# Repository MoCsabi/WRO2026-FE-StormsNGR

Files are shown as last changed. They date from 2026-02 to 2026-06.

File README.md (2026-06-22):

# Introduction
We are the StormsNGR team from Hungary, and we are competing in the 2026 WRO Future Engineers category. This is our third year after two very successful years of competition. You can find our documentation from 2024 [here](https://github.com/MoCsabi/WRO2024-FE-StormsNGR) (🥇) and from 2025 [here](https://github.com/MoCsabi/WRO2025-FE-StormsNGR) (🥉). We will be updating this repository with our progress, which will be documented in our new [Engineering Journal](/Engineering%20Journal.md).

## The team
>Team members
- **Csaba Molnár** from [Budapest University of Technology and Economics](https://www.bme.hu/en) Faculty of Electrical Engineering and Informatics
  - csabi@molnarnet.hu
- **András Gräff** from [Budapest University of Technology and Economics](https://www.bme.hu/en) Faculty of Mechanical Engineering
  - andrasgraff@gmail.com
- **Levente Molnár** from [Vocational Technical School and High School of Biatorbágy](https://en.bit-edu.hu/)
  - levente@molnarnet.hu
>Coach
- József Balázs Gräff
  - graffjozsefb@gmail.com

Links to our socials:

- **Facebook**: https://www.facebook.com/stormsteam/
  - Here you can find updates about the team
- **YouTube**: https://www.youtube.com/channel/UCyzm_Su7qoRCof-ZpbG_9Ig
  - Here you can watch videos about past competitions
- **Instagram**: https://www.instagram.com/storms_team_hun/
  - Cool posts and updates about our, and our sister-team StormsRMS' preparation for upcoming competitions

# Abstract
Our solution is an autonomous car powered by a Raspberry Pi coded in Python, responsible for the main challenge logic, and an ESP microcontroller coded in C, responsible for controlling the motors and processing sensor data. The two devices communicate using UART. We use a 360° 2D LiDAR combined with a gyro to always know where the robot is on the mat. Detection of the traffic sign's color is done by combining the output of the LiDAR with the camera feed to know exactly where the object is. We use ackermann steering geometry calibrated so the car can leave the parking space in one continuous arc. Driving is powered by 1 DC motor through a differential gearbox designed from scratch, with a top speed of around 2.6 m/s.

# Table of contents

### [Our journey](/Our%20Journey.md)
### [Engineering Journal](/Engineering%20Journal.md)
### [Ideas and principles](/Ideas_and_principles.md)
### [Mobility and Mechanical Design, Power and Sensor Architecture documentation](/schemes/README.md)
### [Software Architecture and Obstacle Strategy doscumentation](/src/README.md)
### [measurement- The robot's mechanical characteristics](/The%20robot's%20mechanical%20characteristics.md)
### [RpiCode development tool documentation](/other/README.md)
### [Videos](/video/video.md)
### [Team Photos](/t-photos/)
### [Vehicle Photos](/v-photos/)

# Special thanks
Special thanks to Zsolt Molnár for all the mentoring he's done for us, József Molnár from the [Budapest University of Technology and Economics](https://www.bme.hu/) Faculty of Mechanical Engineering for helping us with the preparations, György Fenyvesi for helping us develop our prototype [custom made interconnect panel](/schemes/README.md/#custom-made-interconnect-panel-wiring-with-connections-labeled), and a bunch of others for helping us by reviewing all the documentation. And of course, to both our families for tolerating us taking up the entire living room with the robot mat 🙂.

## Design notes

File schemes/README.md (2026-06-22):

# Mobility and Mechanical Design, Power and Sensor Architecture
The robot is made up of a lot of different sensors, motors and two processing units, the ESP microcontroller and a Raspberry Pi. The car uses ackermann steering geometry and one DC motor through a motor controller with a differential gearbox we designed and printed from scratch. We had to create a lot of custom 3D printed components and even a custom interconnect panel to help with complicated wiring. The power to the robot is supplied by a 11.1V lithium battery and is later converted to 5V by a step-down module.

## List of components
We installed a lot of sensors and other components on the car, here is a list of each of them with a link and some additional notes:
- **Ackermann steering mechanism** and **base plates** [Ackermann Intelligent Car](https://www.hiwonder.com/collections/robotic-car/products/ackermann-steering-chassis?variant=40382428381271)
  - originally 270 x 197 mm, 960 g
- **Steering servo** [Carson CS-3](https://www.amazon.co.uk/Carson-500502015-500502015-CS-3-Servo-3Kg-JR/dp/B0037Y93CW)
  - Operating voltage 4.8 - 6 V, torque 31 Ncm, operating time 0.17 sec/60° dimensions : 38.5 x 19 x 32 mm, weight: 39 g
- **DC motor** [Hiwonder JGB37-520R30-12](https://www.hiwonder.com/products/hall-encoder-dc-geared-motor)
  -  Operating voltage 12V, torque 15 kg*cm max 3.2A, 280 RPM, 440 pulse-per-revolution encoder
- **Single Board Computer** [Raspberry Pi 5 4GB](https://www.raspberrypi.com/products/raspberry-pi-5/?variant=raspberry-pi-5-4gb)
  - Operating voltage 5V/5A USB-C, 4 USB ports, 40 pins
- **Microcontroller (ESP)** [NodeMCU-32S](https://www.hestore.hu/prod_10037961.html)
  - Operating voltage 5V, 2*19 pins, dimensions: 49.5 x 26 mm
- **Custom interconnect board**
  - ESP pins insert into this, PCB that groups common pins near each other, helps with wiring
- Inertial Measurement Unit (**IMU**/**Gyro**) [BNO085](https://www.hestore.hu/prod_10044901.html)
  - Operating voltage 3.3V, drift 0.5°/min, dynamic rotation error 4.5°
- **Motor driver** [DRV8871-MK](https://www.hestore.hu/prod_10048030.html)
  - Output 3.6 A max
- **Step-down module** [XL4015-3D-STDN-PSU](https://www.hestore.hu/prod_10042112.html)
  - Output 5V/5A, displays voltage, useful for checking battery state
- **Battery**
  - Bundled with Ackermann Intelligent Car, 11.1V, 6000mAh, lithium
- **Display and buttons panel** [Led&Key](https://www.hestore.hu/prod_10042203.html)
  - 8 seven segment displays, buttons, LEDs
- **Active buzzer** [Z2 buzzer (KPI-G2330E)](https://www.hestore.hu/prod_10029469.html)
  - Operating voltage 3-24V DC, 3700 Hz, 83 dB, dimensions ⌀23x10mm
- **Power switch** [ST 1/BK (MRS-1)](https://www.hestore.hu/prod_10023322.html)
  - Dimensions 19.3x12.9mm
- **LiDAR sensor** [STL-19P, D500 development kit](https://www.waveshare.com/wiki/D500_LiDAR_Kit)
  - Dimensions 38.6 x 38.6 x 34.8 mm, range 0.02-12 m, frequency 5-15 Hz, accuracy ±45 mm
- **Camera** [Raspberry Pi Camera Module 3](https://www.raspberrypi.com/products/camera-module-3/)
  - FPC connector, standard lens, RAW10 color format, vertical FOV up to 41°, horizontal up to 66°
- **Ball bearings**
  - 3 pieces of 7(inner diameter)x19x6 mm and 1 piece of 6(inner diameter)x12x4 mm
- **USB-TTL bridge** [CP2102](https://www.ebay.com/itm/203604196200)
  - 3.3V, enables us to use another serial port on the Pi for UART communication
- [**Carbon fiber Lego technic axle**](https://joooooy.com/products/moc-carbon-fiber-technic-axle-4519-3705-32073-3706)
  - can be cut to size, heavy-duty, won't bend as easily
## Assembly - Overview

This section serves as an overview of the design philosophy of the robot. For more details about the actual driving and steering mechanism see [Drive](#drive), and for building instructions see [Building instructions](#building-instructions).

Our robot utilizes ackermann steering geometry and differential drive. We have 3 decks, a bottom deck (or lower deck) for the servo, driving mechanism and the power supply. On the middle deck we have the Raspberry Pi, the main control unit coded in python, responsible for the main challenge logic, and the ESP microcontroller, the secondary control unit coded in C, responsible for receiving sensor data and controlling the motors. The LiDAR sensor is is also mounted here. The third deck is about half the size of the other decks, it houses things like the motor driver, the IMU, the display panel and the step-down PSU.
image showcasing the 3 decks on the robot image of the car with connections between components
(Sketch that illustrates the connections between the different components of the robot)

For steering we used a solution that can be found in many RC cars, we took one from the Ackermann Intelligent Car by HiWonder. After calibrating the geometry to the length of our car we maximalized the steering range to ensure tight turns. We also replaced the steering servo for one with less power consumption and slightly smaller size. For the driving motor we used a 1:10 ratio 12V DC motor and secured it with 90° mounting brackets. The D-shaft of the motor goes inside the custom-designed differential gearbox, where we convert to a lego technic X axle, on which the wheels are mounted. For the rear wheels we used thin Lego wheels, and for the front wheels thin Lego compatible custom 3D printed wheels to make the robot less wide, and make parking easier. Due to the many heavy installments, such as the motor and the power supply, the center of gravity is low, which is ideal for track stability and turning.  
On the middle deck we have the Raspberry Pi and the ESP-32 microcontroller with its pins mounted on a custom interconnect PCB. It helps with the wiring by routing certain pins next to each other and allowing us to use ribbon cables, making everything much cleaner. This deck is separated from heavy-duty equipment like the motor which cause electrical noise that could interfere with the controllers. The LiDAR sensor is also mounted here with a special mounting bracket, ensuring the widest FOV possible. The base of the camera tower is also mounted here.  
The third deck is much smaller, the main reason we installed it was the lack of space for the remaining components, while also keeping the car small and light. Importantly the Led&Key input and display panel is also installed here for easy access. The camera tower ensures the camera is looking in front of the robot with a 15° vertical tilt down. The final size of the robot is 26.8 cm long, 15.8 cm wide and 20.9 cm high. It weighs 1246 grams.

## Sensors
We use many sensors to explore the field, detect the traffic signs and keep track of the robot's position.
### Encoder
Possibly the simplest sensor we utilize, it measures the DC motor's direction and rotation, using a magnetic AB encoder. The ESP micrcontroller listens to the interrupts generated on these pins and calculates the actual speed of the robot alongside it's direction. This is measured in "ticks" and "ticks"/second, an arbitrary unit with relation to traveled distance, defined by the motor's and the differential's ratio among other factors. We now have to convert these "ticks" to centimeters. We tested and calibrated this value to be excatly `14 "ticks" per cm`, which is a good enough resolution. The calculated speed (signed value) is then sent over to the Raspberry Pi. We mainly use this sensor to measure the speed of the robot but there are situations where we can't rely on the LiDAR so we use the encoder to travel for certain centimeters.
### IMU
The Inertial Measurement Unit, sometimes referred to as the gyro is responsible for keeping track of the robot's direction. We wanted an IMU that's capable of calculating the heading angle on board, instead of us having to do it manually, by integrating the angular velocity and applying complicated filters. This way we had one less challenge to solve. It also had to stay reliable during the entire 3 laps. Our first choice of gyro, the MPU-6050 didn't have on-board heading calculation, so we looked for sensors that do. This is how we found the `BNO085`. This sensor satisfied both requirements with a ~2-3° of dynamic error over the 3 laps and excellent on-board angle calculation. In RVC mode the gyro simply sends the heading data over to the ESP 100 times a second which the ESP forwards to the Raspberry Pi. It did have a pretty big static turning angle error, meaning every 90° it gets offset by 1°. But this can be measured, tested, and corrected with a constant multiplier to the angle, right on the ESP, so the Pi receives the already correct angles. More about how exactly this problem was solved in the [Software Architecture and Obstacle Strategy documentation/Sensors and motors](/src/README.md#Sensors-and-motors).
### LiDAR
Arguably our most important sensor, a 2D 360° LiDAR sensor. The requirements when choosing the sensor were a range of at least 3m and an accuracy of 2-3 cm. Based on the available datasheets we chose the STL-19P from the D500 development kit. It came with an UART to USB converter board which was useful in the initial setup phase. It's a TOF (time-of-flight) LiDAR, meaning it spins a laser emitter really fast and compares the return time of the laser to the speed of light to calculate the travelled distance. We soon realized the scanning frequency (rotation speed) and ranging frequency (sample rate) are also critical parameters. The base scanning frequency was 10 Hz, so every angle's distance gets refreshed 10 times a second. On the default speed of the robot this translates to ~4-5 cm jumps between measurements. This is not ideal, as we use this sensor with the IMU to measure the distance from the front wall for example to start arcing at a specific point, and 5 cm deviations can lead serious problems. Thankfully this 10 Hz can be sped up to 15 Hz, which greatly reduces this problem, however introduces another. Since the sample rate of the sensor is a fixed 5000 Hz, with 15 Hz scanning frequency that means the angular resolution goes above 1° (360°*15Hz/5000Hz=1,08°), meaning not every degree gets refreshed every turn. This is compensated for in software, more details in the [Software Architecture and Obstacle Strategy documentation/Sensors and motors](/src/README.md#Sensors-and-motors). We also had to write our own library to parse the inputs of the sensor, more about this in the aforementioned documentation.

This sensor is responsible for exploring the field, such as detecting walls and traffic signs. Combined with the IMU it can always tell the distance to the front wall, a function we heavily rely on.
### Camera
With the aforementioned sensors only we are missing one crucial information: the color of the traffic signs in obstacle challenge. For this we had to get a camera. We use the Raspberry Pi Camera Module 3, for the ease of integration with the main control unit the Raspberry Pi. Currently we only use the camera for this purpose, to look at an area speicified by the LiDAR and average the pixels, then decide if it's more green or more red.
### Calibration and tests
We have a long list of calibration procedures and tests, some having to be done before every round, while most only after a reassembly.
- Before starting a round the robot has to be straight. We define straight as the rear axle of the robot has to be perpendicular to the walls. But it would be hard to position it based on that, we instead opt to position the robot so it's side is parallel to the walls. This is easier as it's a bigger surface and we can easily access it. But for this to work the side of the robot has to be perpendicular to the rear axle, meaning in our case the two wheels on the side have to be precisely positioned with spacers to form this line.
- The steering servo has to be calibrated after small mechanical changes. We calibrate 3 PWM values, the center state, the leftmost state and the rightmost state. When calibrating the outermost states we balance between keeping turning simmetrical and maximizing turn angles. Of course we are also make sure not to stall the servo as that could cause a meltdown.
- The LiDAR is mounted on the middle deck, and any amount of sideways tilt can cause the sensor to see into the ground on one side causing detecting errors. To avoid this the spacers on the side of the robot have to be installed evenly. This needs testing every time there's a reassembly.
- The LiDAR sensor's forward angle also has to be calibrated. This is because it's not perfectly mounted, the angle the sensor refers to as 0° is in reality something like 1-2°. This is combatted via a constant, which has to be recalibrated after major reassemblies.
- The IMU sensor has to be standing still when powering on the robot to ensure proper built-in calibration. There is also the static turning angle error which is combatted by a constant multiplier, this only has to be calibrated once per sensor we found.
- We also have to calibrate the camera's positioning relative to the LiDAR, as mapping the object found by the LiDAR to the camera space is critical for the obstacle challenge. This is achieved with a number of constants, relating to the position and rotation of the camera relative to the LiDAR. This only needs recalibrating during major reassemblies or restructurings.

Before competitions we make sure to run through this list, even the ones normally only necessary after major changes.
## Connections
The different connections used between the components of the robot and their hierarchy:
- Computer
  - Raspberry Pi `SSH`
    - ESP `UART` Pi: **USB-TTL** - ESP: **RXD-GPIO-25, TXD-GPIO-26**
      - IMU `UART-RVC` **(SDA-GPIO 17)**
      - Motor encoder `Digital` **(A-GPIO 34, B-GPIO 35)**
      - Motor driver 2x`PWM` **(PWM_1-GPIO 13, PWM_2-GPIO 16)**
      - Servo `PWM` **(Signal-GPIO 27)**
    - LiDAR `UART` **(TX-GPIO 15)** 
    - Led&Key panel `Data, Strobe, Clock` **(DIO-GPIO 19, STB-GPIO 16, CLK-GPIO 13)**
    - Buzzer `Digital` **(+-GPIO 5)**
    - Camera `FFC`

The actual communication between the components is detailed in the [software documentation](/src/README.md#sensors-and-motors).
## Wiring diagrams
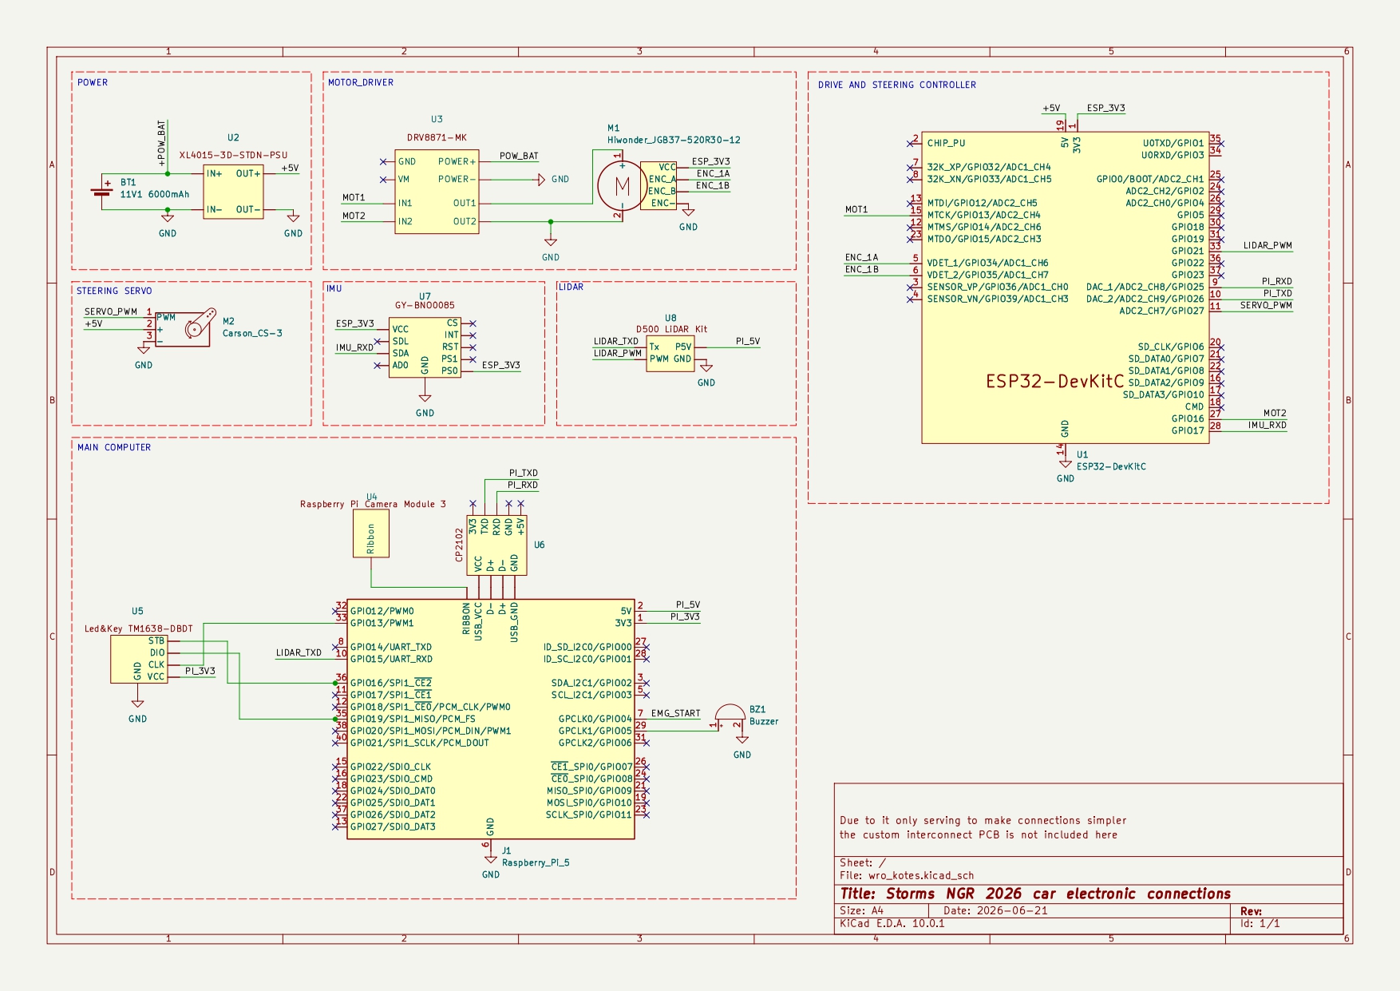
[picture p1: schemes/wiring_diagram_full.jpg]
full wiring diagram
  
The complete wiring diagram of the robot, including the Raspberry Pi, the ESP, the two motors and the sensors.

The diagrams below serve more as a cabling guide, with the colored squares representing the cable colors on the robot.
### ESP microcontroller (NodeMCU) pinout with connections labeled:
This illustration is most important for the source code, since everything is actually wired through the custom-made board for the ESP.
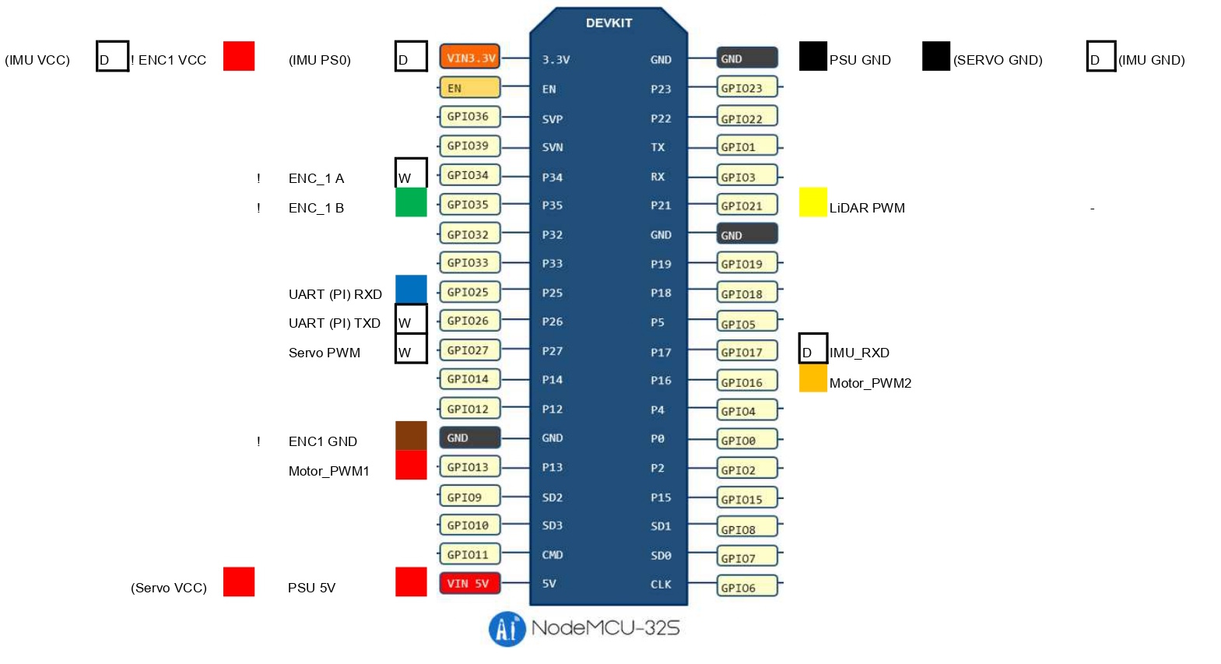
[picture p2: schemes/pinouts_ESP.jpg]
ESP wiring diagram

(ENC-Motor encoder, PI-Raspberry Pi, D: directly connected, !: not wired through the interconnect panel)

### Raspberry Pi pinout with connections labeled:
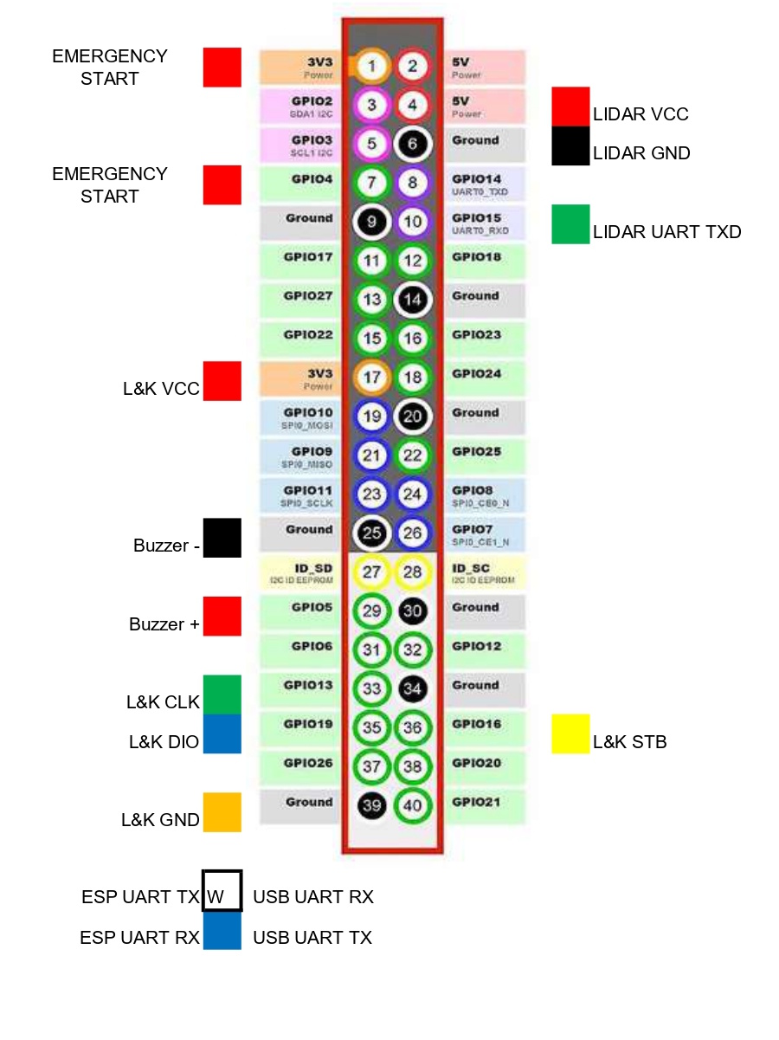
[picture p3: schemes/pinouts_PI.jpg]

(L&K-Led and Key panel)
### Motor controller wiring:
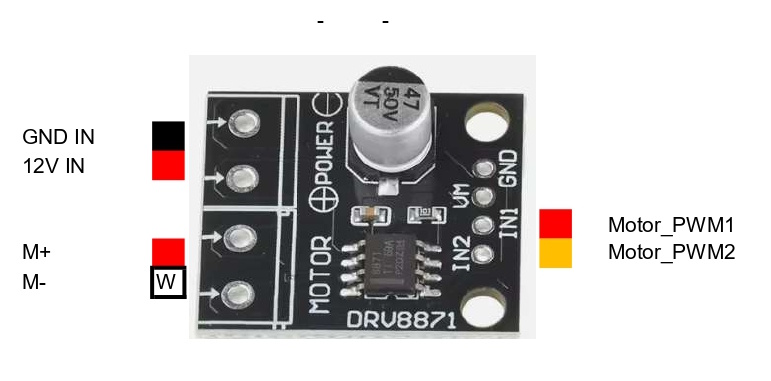
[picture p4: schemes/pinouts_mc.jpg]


All of these can also be found in the form of an excel spreadsheet in the [pinouts.xlsx](pinouts.xlsx) document.

### Custom interconnect PCB schematic and wiring:

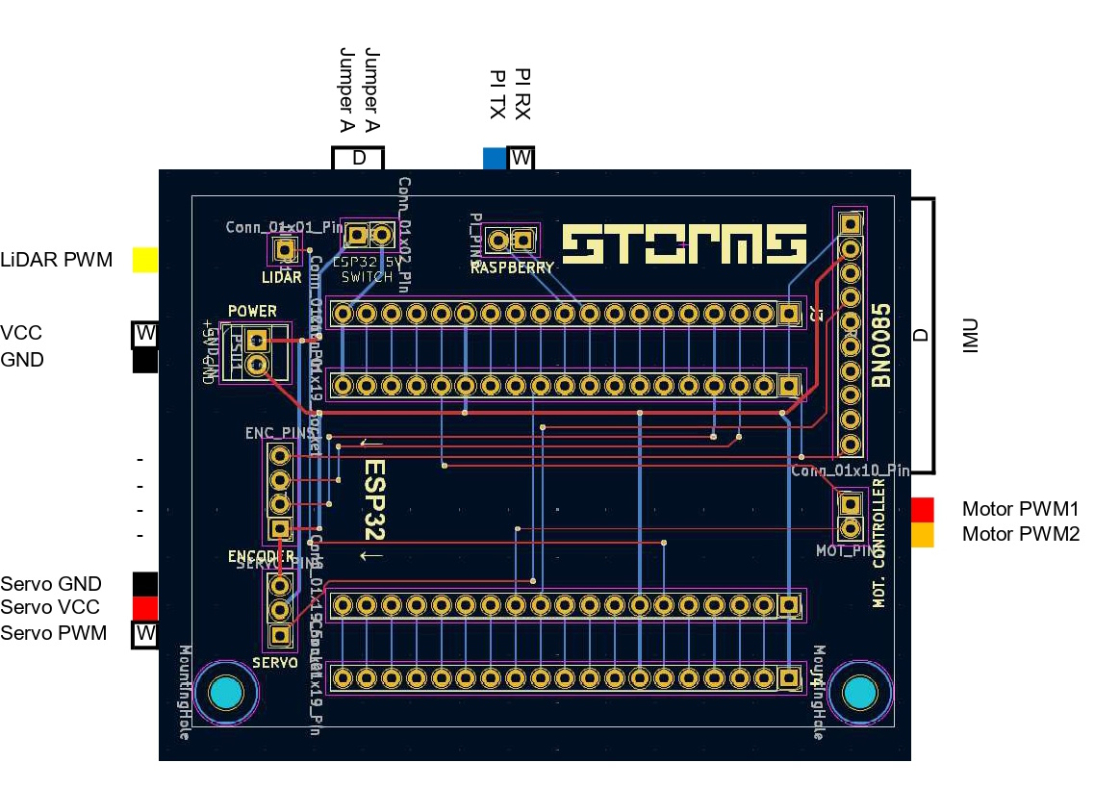
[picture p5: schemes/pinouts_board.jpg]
PCB pinout


*Note: the red wires are on the top, the blue ones are on the bottom of the PCB, which let us connect everything in a clear, simple matrix layout without collisions*

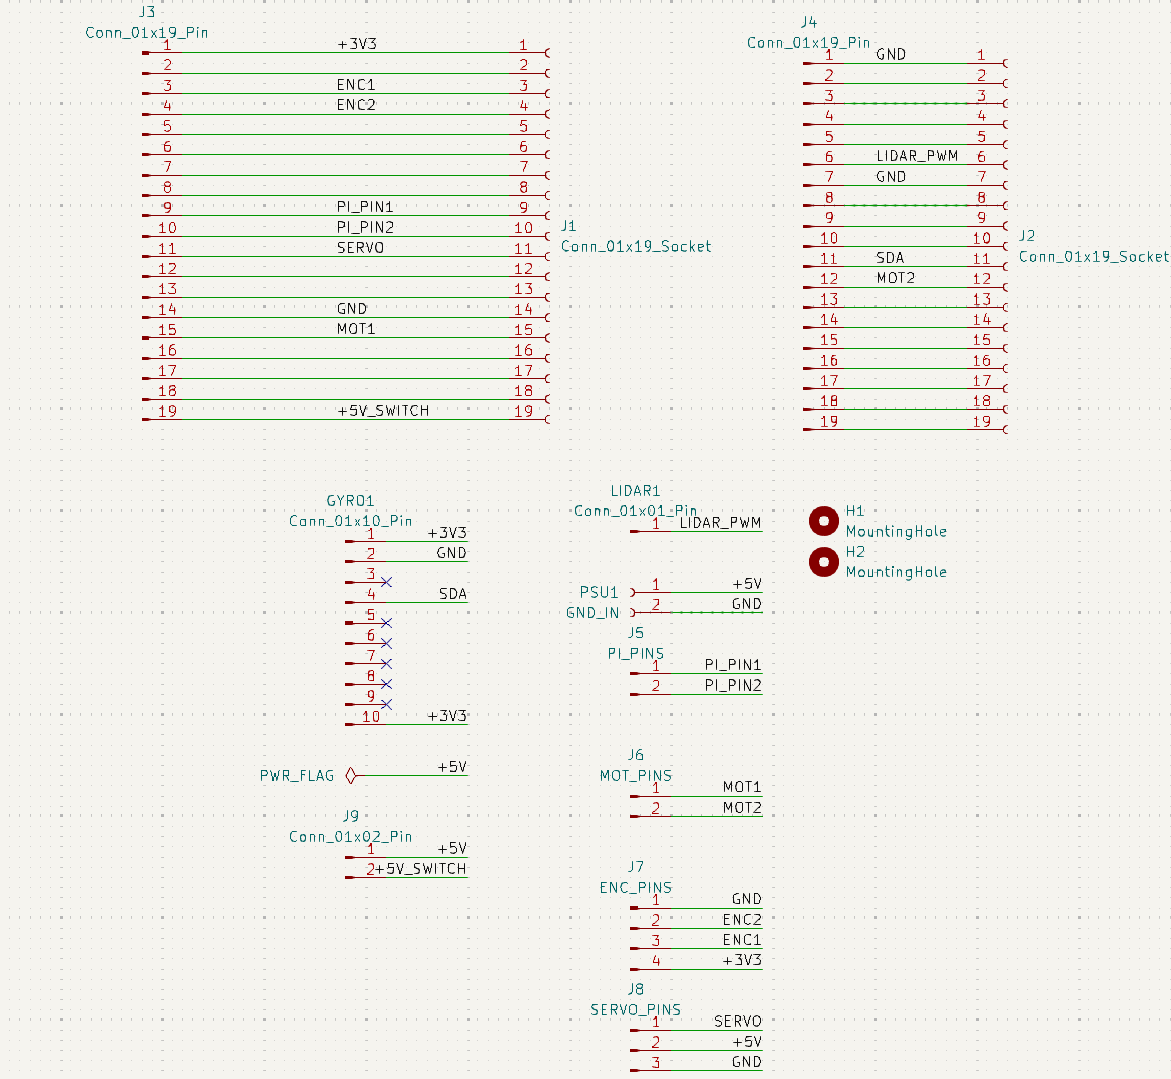
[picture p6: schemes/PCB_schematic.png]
PCB interconnect wiring


Some extra rules had to be employed in order to ensure the PCB working properly. First, the GND and +3V3 as well as +5V wires were thickened, since they deliver much more current than everything else. Another big factor was the 5V wiring itself: the ESP could either get its 5 volt power through the built in pin or USB-C port, but not both without that causing issues (for example, it managed to break the USB port of two of our ESP-s). Because of this, a jumper bridge has been added, if the `ESP32 5V SWITCH` pins are not connected, the ESP must be supplied through the USB port, otherwise power delivery is done through the dedicated pin.

The PCB project, along with its BOM can be found in the [schemes/wro_nyak](/schemes/wro-nyak/) subfolder.

## Power
The robot's power supply is provided by a central accumulator (battery).
We considered powering the motors and the control system from separate power sources due to their differing requirements and to limit the electrical interference (noise), but ultimately decided on a common power source for simplicity. The 11.1 V, 6000 mAh lithium accumulator provides more than sufficient capacity for us. A lower capacity device would have also sufficed and while being lighter, but the ability to avoid constant recharging is a great advantage for us during the testing periods. We also don't mind the significant overhead as it allows us to not have to worry about having enough power. For safety, the accumulator is easily removable via a detachable cable. We have a spare unit, enabling us to charge one while using the other. The accumulator connects directly to the main switch via the detachable cable.
The battery's largest consumer is the drive motor. The DC motor connects to the motor driver without voltage conversion. The driver's maximum current is 3.6A, which is sufficient for the motor's maximum current draw of 3.2A. The motor driver includes essential integrated protections (Overcurrent Protection - OCP, Thermal Shutdown - TSD).
The remaining components of the system operate at 5V, which we provide using a step-down power supply. A very useful feature of this power supply is that it displays the input voltage, allowing us to monitor the battery's state of charge. Among the 5V components, the Servo and the Raspberry Pi require significant current, which is handled by the power supply's 5A maximum current output.
A few of the robot's components, mainly sensors, operate at a 3.3V voltage level, but their power supply is provided by the controller (ESP/Pi) they are connected to.

A simple explanation of the power supply hierarchy of our robot.
- Battery `12V`, max. **6A**✅ [`55,73W`/72W]
  - Step-down module `12V-->5V` max. **5A**✅ [`17,33W`/25W] 
    - Steering servo `5V`, **200mA** (stall: 1,2A) [max. `6W`]
    - Raspberry Pi 5 `5V` (from USB-C, can supply `3.3V`), **~1200mA** [`6W`]
      - LiDAR `5V`, **290mA** [`1,45W`]
      - Camera `5V` **200mA** (FFC) [`1W`]
      - Led&Key Panel `3.3V`, **100mA** [`0,33W`]
    - NodeMCU-32S `5V` (from **Vin** pin, can supply `3.3V`), **500mA** [`2,5W`]
      - Inertial Measurement Unit `3.3V`, **5mA** [`0,02W`]
      - Motor encoder `3.3V`, **10mA** [`0,03W`]
  - Motor driver `12V`, max. **3,6A**✅ [`38,4W`/43,2W]
    - DC motor `12V` **~1A** (stall: 3.2A) [max. `38,4W`]

In the square brackets we calculated the maximum power consumption, which would happen if both the servos and the DC motor was stalling. As you can see we have more than enough power and current. We do have to be careful with stalling as this can cause the motors to melt-down. Short-circuiting can cause very high current that our jumper cables can't handle, causing them to melt. We have to watch out for these dangers as they and have caused long-term damage, we lost a servo and a DC motor this way.
## Drive
For steering, we utilize Ackerman steering geometry.
In short, the inner wheel turn slightly more than the other, so the robot stays on the same arc without any slippage. Here's an image from the [Hiwonder documentation](https://drive.google.com/drive/folders/11k0gbcZExI4076KJ1d_CCIdDlopuYUwO) that illustrates the principle:

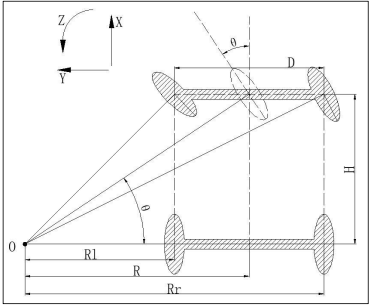
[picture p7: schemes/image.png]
ackerman geometry


The steering mechanism has to be assembled so the steering pivots are on the line between the steering kingpin and the center of the rear axle.

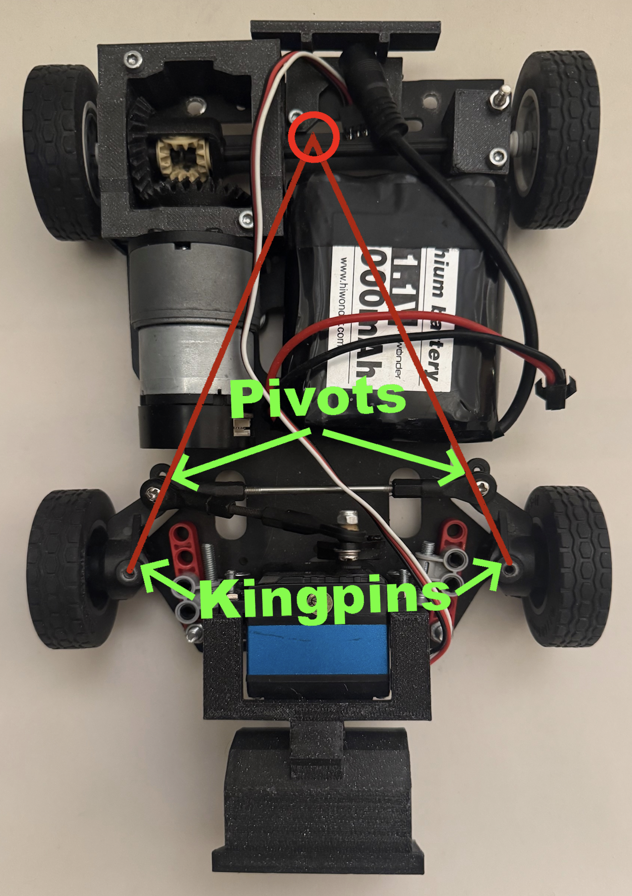
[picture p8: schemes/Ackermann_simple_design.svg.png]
ackermann geometry illustrated


We use two kinds of turning, turning along an arc or turning until a target degree is reached using **PID** control with the gyro. For turning along an arc we can use this formula to calculate the correct servo angle for an arc given $R$ radius:
$$θ=arctan \left( {H \over R} \right)$$
($H$-distance between front and rear axles, $R$-target radius)

For driving we wanted to use [Electronic Differential](https://en.wikipedia.org/wiki/Electronic_differential), which is simply simulating a differential using software by calculating the required force using the current angle of the servo.
The formula for calculating the correct speeds of the two motors:
$${V_l}=\frac V R*\left( R-\frac D 2 \right)$$
$${V_r}=\frac V R*\left( R+\frac D 2 \right)$$

($V_l$- left motor speed, $V_r$- right motor speed, $R$- current arc, $V$- robot tangential speed)

This would have been the most ideal solution, as this way we could avoid complicated hardware components and also use the power of 2 DC motors easily. This is also how many modern real life electric cars operate (such as the [Tesla Model S](https://en.wikipedia.org/wiki/Tesla_Model_S#Powertrain) for example), and since the competition's main goal with car restrictions seem to be realism we hoped this solution would be accepted. However, with the reasoning that cheating by not accurately simulating a differential would be hard to detect, this solution was not allowed by the head judges. This way we had to design and 3D print a differential gearbox from scratch, and only use 1 DC motor. 

First, we created a mechatronic model of the drivetrain starting from the motor to the wheels.
The so-called mechanical impedances of the components ($Z_{force} = \frac{1}{m\cdot s}, Z_{torque}=\frac{1}{J\cdot s}$ in the Laplace domain)

Impedance network of the car's drivetrain

From this, using a Jupyter notebook, all the parameters of the system could be calculated.
The moments of inertia were generated using the `numpy-stl` library, the rest were of the values were measured manually. From this we concluded that with the current setup the transmission ratio should be changed as much as possible to favor lower torques and higher rpm. We designed two helix gears with 1:1 transmission with Lego technic axle slots for heavy duty carbon fiber axles, which gave us more than enough maximum speed at 2.6 m/s. We made sure to use ball bearings where the axles are supposed to rotate freely. The design process is further detailed in [The design process of 3D printed parts](#the-design-process-of-3d-printed-parts). A simple diagram showing this solution:

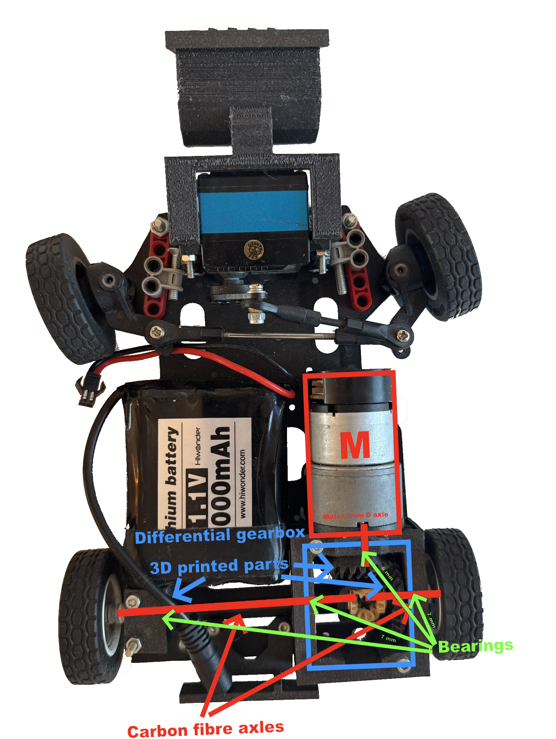
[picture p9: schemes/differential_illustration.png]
diagram


($M$- DC Motor)

# The design process of 3D printed parts

Designing and printing out different parts of the robot was one of our biggest task where we had to take a lot of things into account in order **for everything to work properly**. Sometimes we had to rely on **trial and error** to make sure everything was how we wanted it to be.

---

## The steps of The design process:

### 1. Coming up with the general shape and location of the part
  
  In This part we first had to take a close look at how our robot looked so far then try to figure out **how and where our soon to be designed part could fit.**
  Things we had to look out for:
  - Having an appropriate amount of space for the parts.
  - Having the right screw holes to be able to make a good mounting mechanism.
  - Making sure that putting the part there wouldn't interfere with anything else.
  
  After we found to correct location we made a very, **very simplistic sketch** of what we wanted.

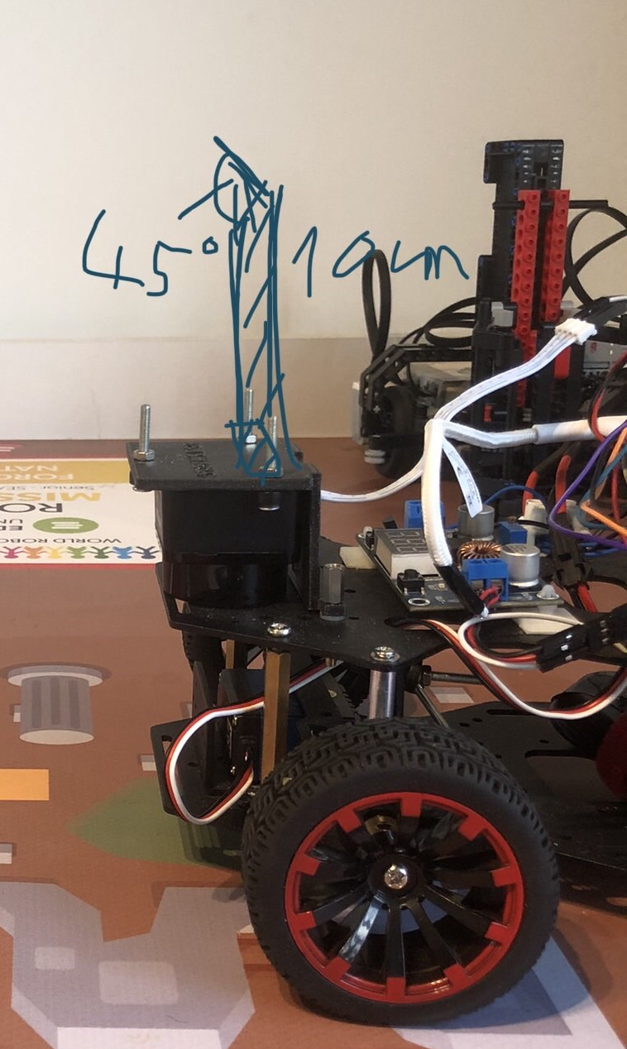
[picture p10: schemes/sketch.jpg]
Sketch for the camera stand
  

### 2. Gathering usable documentation
  This is maybe the most important part in the process, because the quality of the documentation available **can make or break a design**. While taking your own measurements is viable, it is a lot simpler to use a documentation and yields **more precise results**.

### 3. Making the model
  We used *Autodesk Fusion 360* for designing our parts, however any industrial software like *Autodesk Inventor* can be used as well. In the modelling process there are a couple of things to remember:
  
  - Make sure that any measurement given in a documentation seems realistic, **since we have seen mistakes even in official documentations**.
  - Always double check any calculation and check the dimensions relative to multiple sides, because **it may look alright from one side, but may be completely unusable from another**.
  - Use your software's built in physics simulators to check for weak points and **always make sure it can handle the stress it may be placed under**.
  - When done export the file as an **.stl** so that a slicer can use it.

  Don't worry if you don't know how to make 3D models yet, it is a lot easier than people might think. The process in simple terms just requires you to make a sketch/blueprint like below and extrude it out into 3D space.
  
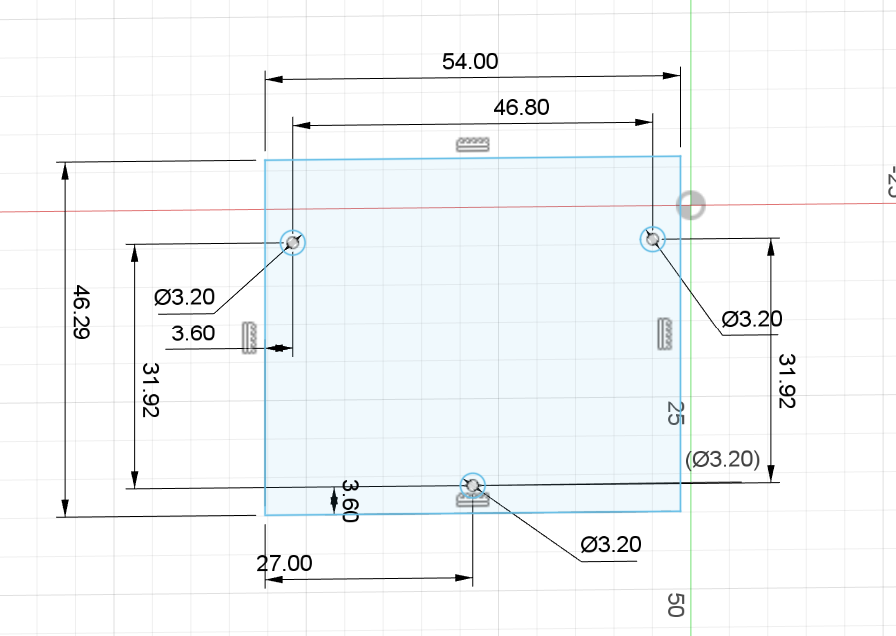
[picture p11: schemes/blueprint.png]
Example of a sketch in Fusion 360
  
  
### 4. Exporting the G-code
  We printed our parts with a *PRUSA mini+* and used *PrusaSlicer*, but any 3D printer and software will do as long as it has a **large enough print area** and supports the **right types of filament** (we use PLA but PETG should also work). We suggest that for more **aesthetic parts a 30% infill** is used and for **more structural ones a 60%**. It may also seem trivial but the **angle and orientation** in which the part is printed matters a lot to. For example **for tires a $45°$ tilt** is suggested to make sure that it **won't come apart parallel to the print lines.**

### 5. Printing out the part
  Here there is not much to look out for, just make sure that the **printer's settings are right,** there is enough filament and the **supports are sufficient.**

---

## How we applied these steps and the difficulties we faced

### The lidar mount

  The lidar mount was the *first part* which we designed ourselves and the part that makes it so that the lidar can see **exactly what we want it to see.** While the robot chassis had the right screw holes to mount it to begin with, the problem we faced relied on the angle in which the lidar shoots out its beams of light. It was slightly angled to shoot upwards. Because of this the lidar was **seeing above the walls** of the map which was a lot less than optimal. Our solution was to flip the lidar upside down to **lower the starting point of the beams and make them shoot slightly downwards instead.**
  The main things we had to look out for in this part were:
  
  > **Making sure that it won't start tilting in random directions throughout the round.**
  
  The way we solved this was, that the mount just makes it so that it doesn't move horizontally, but vertically it doesn't give much support, **letting it lie directly flat on the vehicle**.

  > **Mounting it securely while leaving enough space for a wide field of view.**

  We solved this by only mounting it from the back with two screws, which does give up a lot of stability, but we **still found it sufficient for this use case**.

  > **Making the range of the Lidar as wide as possible while also allowing it to see backwards**

  This was the easiest since we just had to have an empty slot in the back of the mount.

  [The documentation we used (Page 7 is the most important)](https://www.ldrobot.com/images/2023/05/23/LDROBOT_LD19_Datasheet_EN_v2.6_Q1JXIRVq.pdf)

  This part worked flawlessly so we have been using it ever since last year's competition.

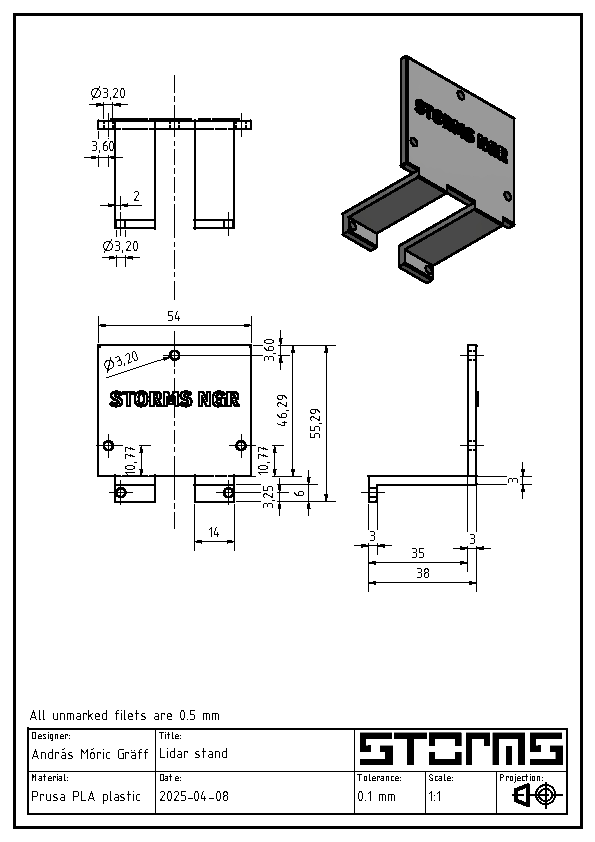
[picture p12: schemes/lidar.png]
Lidar mount
  

### The camera stand
  
  The camera stand was one of the parts that needed an almost complete redesign over last year, but this time it did not require four iterations to get the final result.
  The mounting area stayed the same, using two screws for security and having the main body elevated in order to **allow the Lidar's laser to pass through below it.**
  The top part however required a complete redesign since we changed cameras. It needed to keep the camera at a **height of 20 cm with a depression angle of 15°** to get the correct image. This made the piece quite tall, so a few security bars were added for support. To mount the camera we made small pins that fit exactly into the screw holes of the camera. To make it so that it doesn't fall out, a lid can be slotted in from the top. Between the lid and the camera we also inserted a few pieces of paper to cushion it and make sure nothing gets damaged.

  [The blueprint we used](https://datasheets.raspberrypi.com/camera/camera-module-3-wide-mechanical-drawing.pdf)  
  [Link to the original version](https://github.com/MoCsabi/WRO2024-FE-StormsNGR/blob/main/schemes/README.md#the-camera-stand)

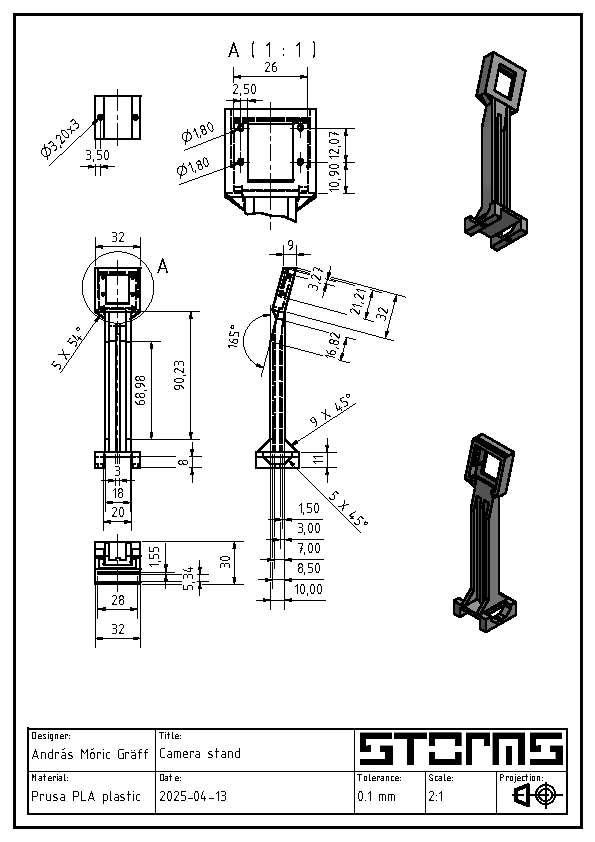
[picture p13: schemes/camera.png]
camera stand
  

  The lid is as simple as this, so it doesn't even need to be 3D printed, a piece of cardboard would work just as fine.
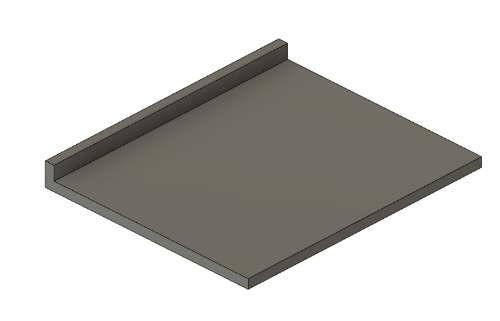
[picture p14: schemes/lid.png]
The lid
  

### The tunnel
  We previously adjusted the lidar mount and camera stand to enable the **lidar to see backwards,** however another part was needed to be designed to make sure that **nothing obstructed the view.** This was the most simple model we ever made, since it really is just a **little tunnel** meant to clear the way.
  
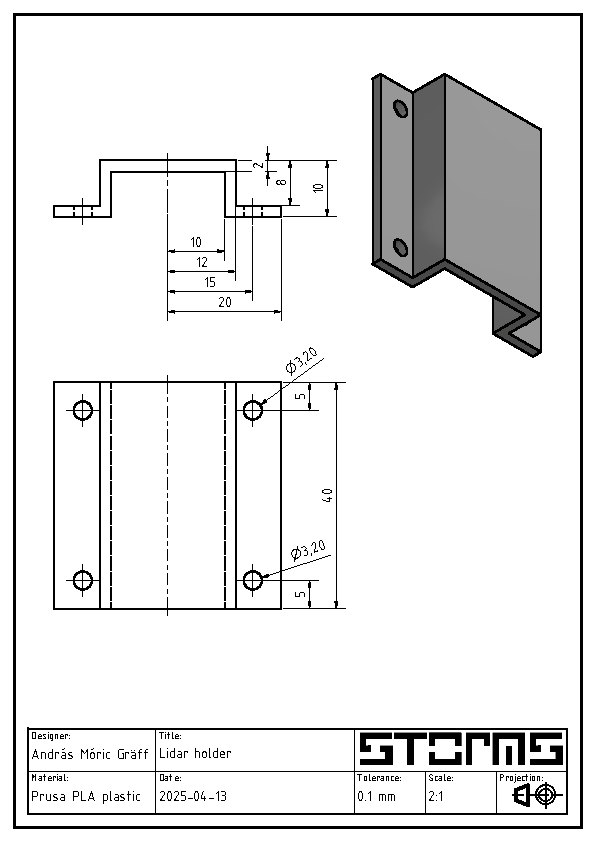
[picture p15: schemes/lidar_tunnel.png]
lidar tunnel
  
  
  It is mounted using four screws, which is a bit of an **overkill,** since realistically it won't really be put under any stress. Because of this we only ended up putting screws into the two rear holes.

### The differential gear
  We decided to make a custom differential and replace the original Lego one. This model required by far the most engineering knowledge.
  The differential was designed with a few important factors considered:
  >-  **To have a size similar to the previous so it would be easier to implement into the assembly.**
  >-  **To have enough tolerances for 3D printing, but at the same time to minimize the backlash between the various gears and - of course - to achieve maximum efficiency.**

  In order to achieve this, we decided to use two helical gears, with one replacing the gear part of the old differential, while not changing the rest. The helical gears allow for better contact between the gears, and therefore a **higher efficiency when the car goes forwards.** Size wise both gears are the same size now (due to the 1:1 gear ratio), their diameters are about equal to the bigger gear in the old differential, so the main axle could stay almost identical to before, with only the motor's position changing slightly.

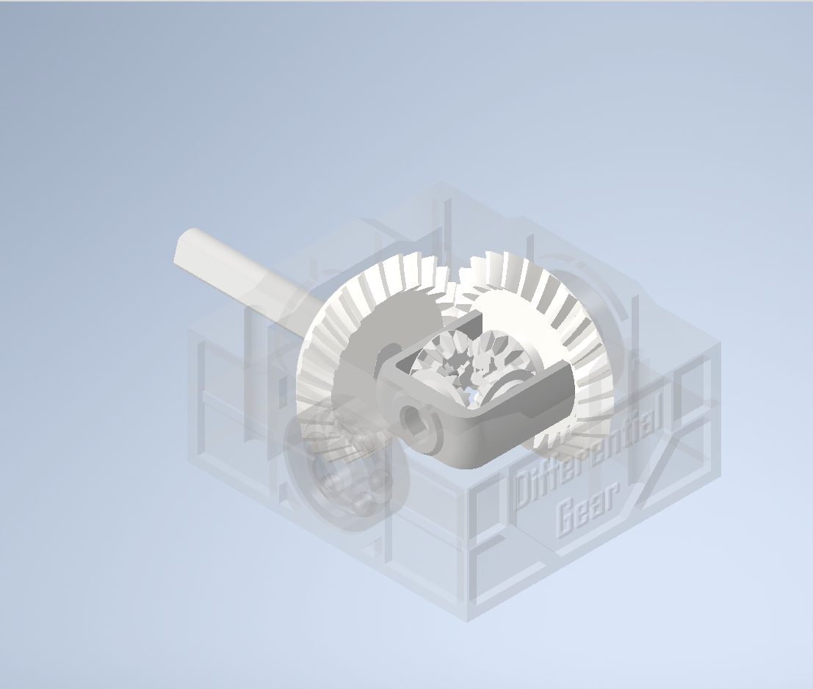
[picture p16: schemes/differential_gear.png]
differential gear
  

### The differential gear frame
  With a new differential we also required a new frame for said differential. The frame is what holds differential in the air so that it doesn't touch anything, and **has embedded bearings to reduce the friction** between the frame and the axles. We used bearings last year as well but this year we made a few improvements in that area.

  >- **Made the slots larger that can accompany larger bearings that provide more support and enables the usage of fitting rings on the axles.**
  >- **Split the model into two and added walls for the slots to make the bearings and the fitting rings unable to move.**

  These changes made the frame a lot more secure, since we had problems with the bearings and axles shifting previously.

  [Link to the original version](https://github.com/MoCsabi/WRO2024-FE-StormsNGR/blob/main/schemes/README.md#the-differential-gear-frame)

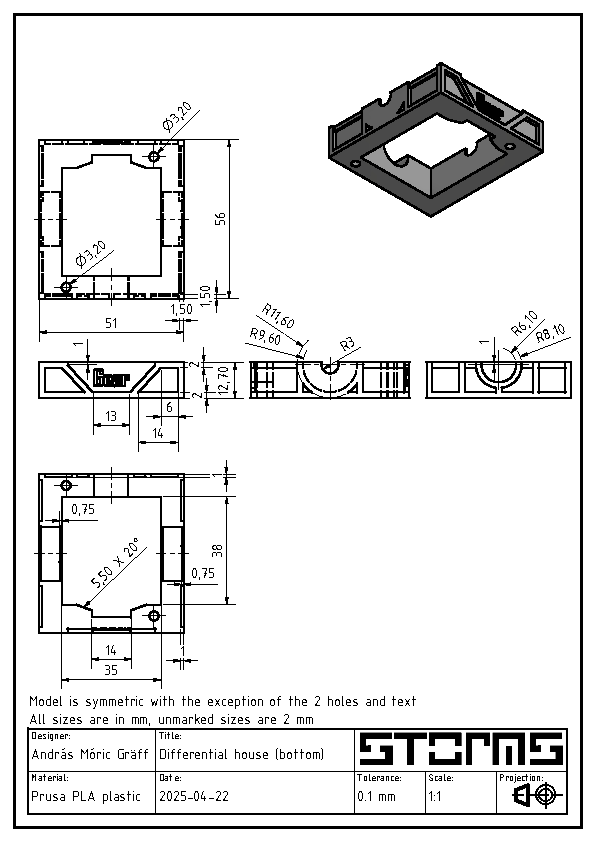
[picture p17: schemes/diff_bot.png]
bottom of the differential
  
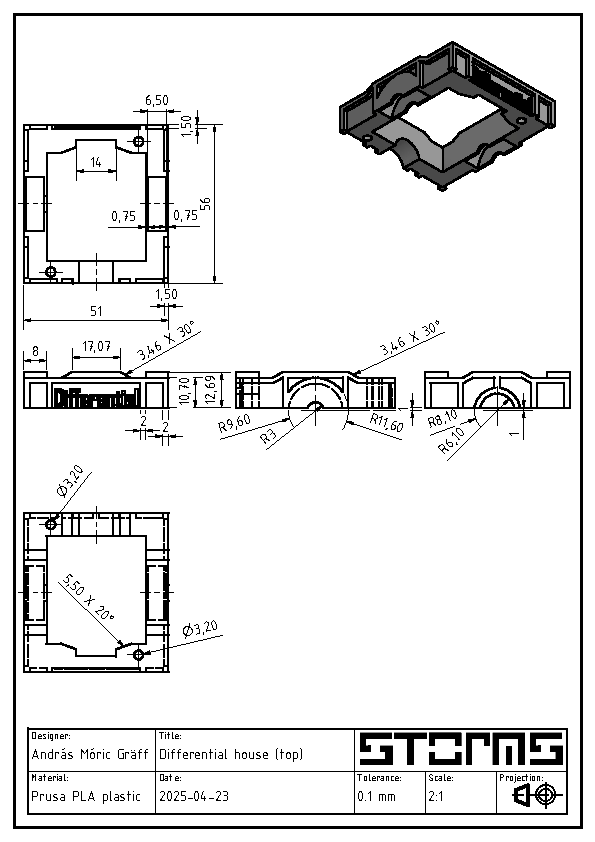
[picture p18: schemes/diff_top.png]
top of the differential
  

### The assembly of the full differential gear

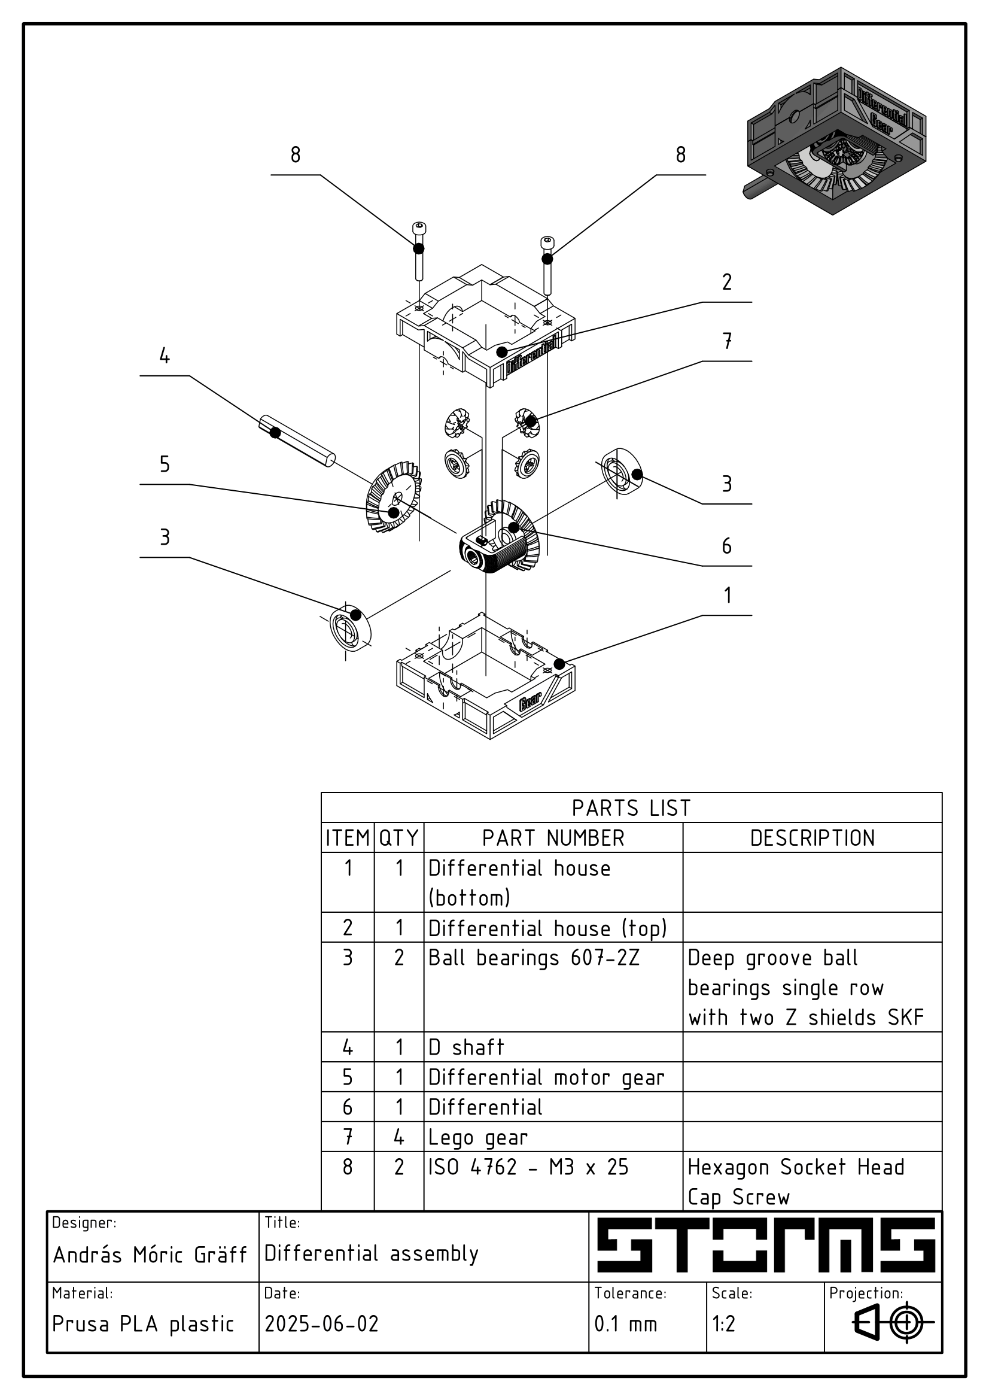
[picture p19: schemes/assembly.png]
differential gear assembly


### Accessories for the differential gear

  The differential gear and house works as is just fine, but for our use case we needed a few extras for it.

#### The fitting rings

  As mentioned above, the axles we used required fitting rings in order to fit cleanly into the bearings. The rings then were glued onto the axles, and since the frame restricts the movement of the ring, this makes it so that the **entire axle can only be moved if the frame itself is disassembled.**

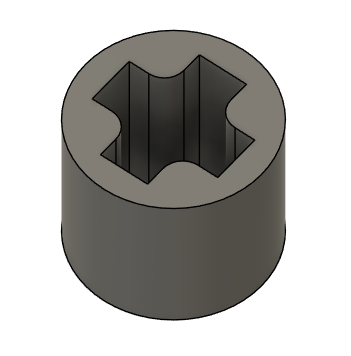
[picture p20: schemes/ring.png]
fitting ring
  

#### The axle holder

  In our robot the differential was on the right side, one of the axles needed to be exceptionally long which would enlarge any potential bending. To counter this we made a securing device which is basically just a box with a bearing in it. Just like the frame, **this was also split in two,** but since this part is completely symmetrical, it only requires one model.

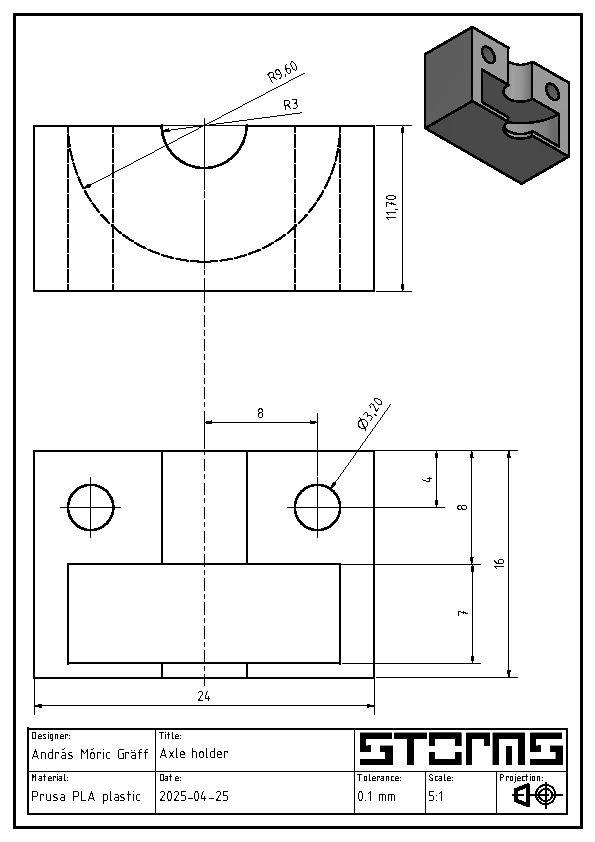
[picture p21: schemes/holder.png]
axle holder
  

### The new wheel

As mentioned before, to save parking space, we decided to switch to thinner wheels, but that caused problems on the front, when mounting. To fix this, we found an STL file of the rims we used online and modified it. We only made two small adjustments.

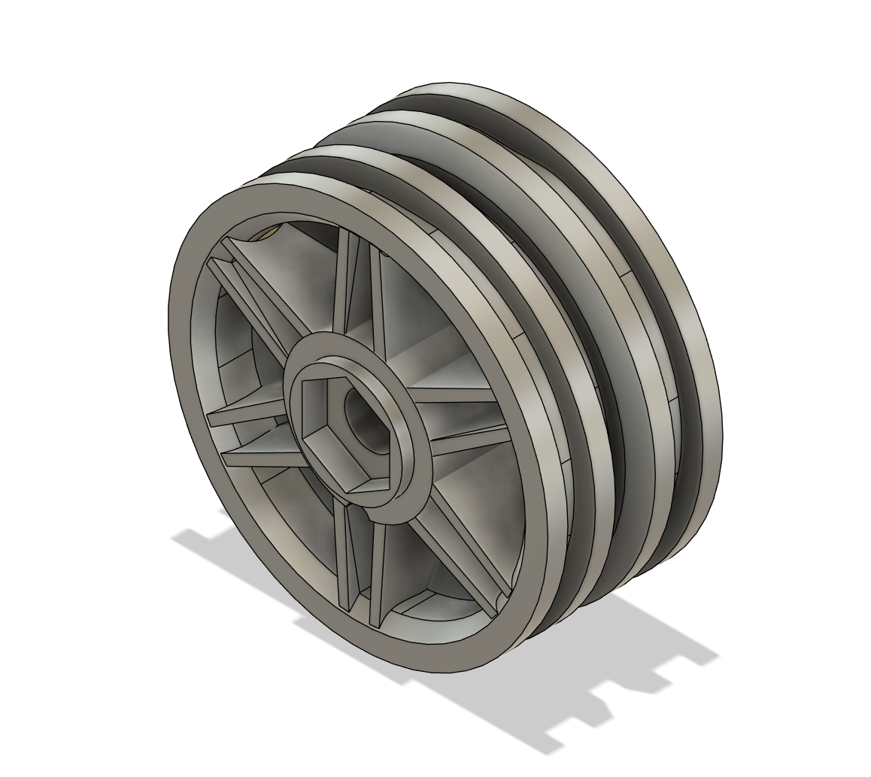
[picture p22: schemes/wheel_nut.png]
new rim


>- **We filled the axle hole in the middle of the wheel and inserted a circular hole that an M4 screw can fit through.**
>- **Addded a hexagonal indent to the outside which can fit an M4 nut.**

Applying these adjustments made the mounting of the front wheels a lot more secure, and also made them take a more straight path on the road, whereas before, there was a slight wobble when going straight.

We also printed a set of default rims for the back, but that was only, so that the colors would match.

### Aesthetic pieces

Last year, for aesthetics we put a shovel in the front of the car, but this year we decided to use a more **modular design** instead.  

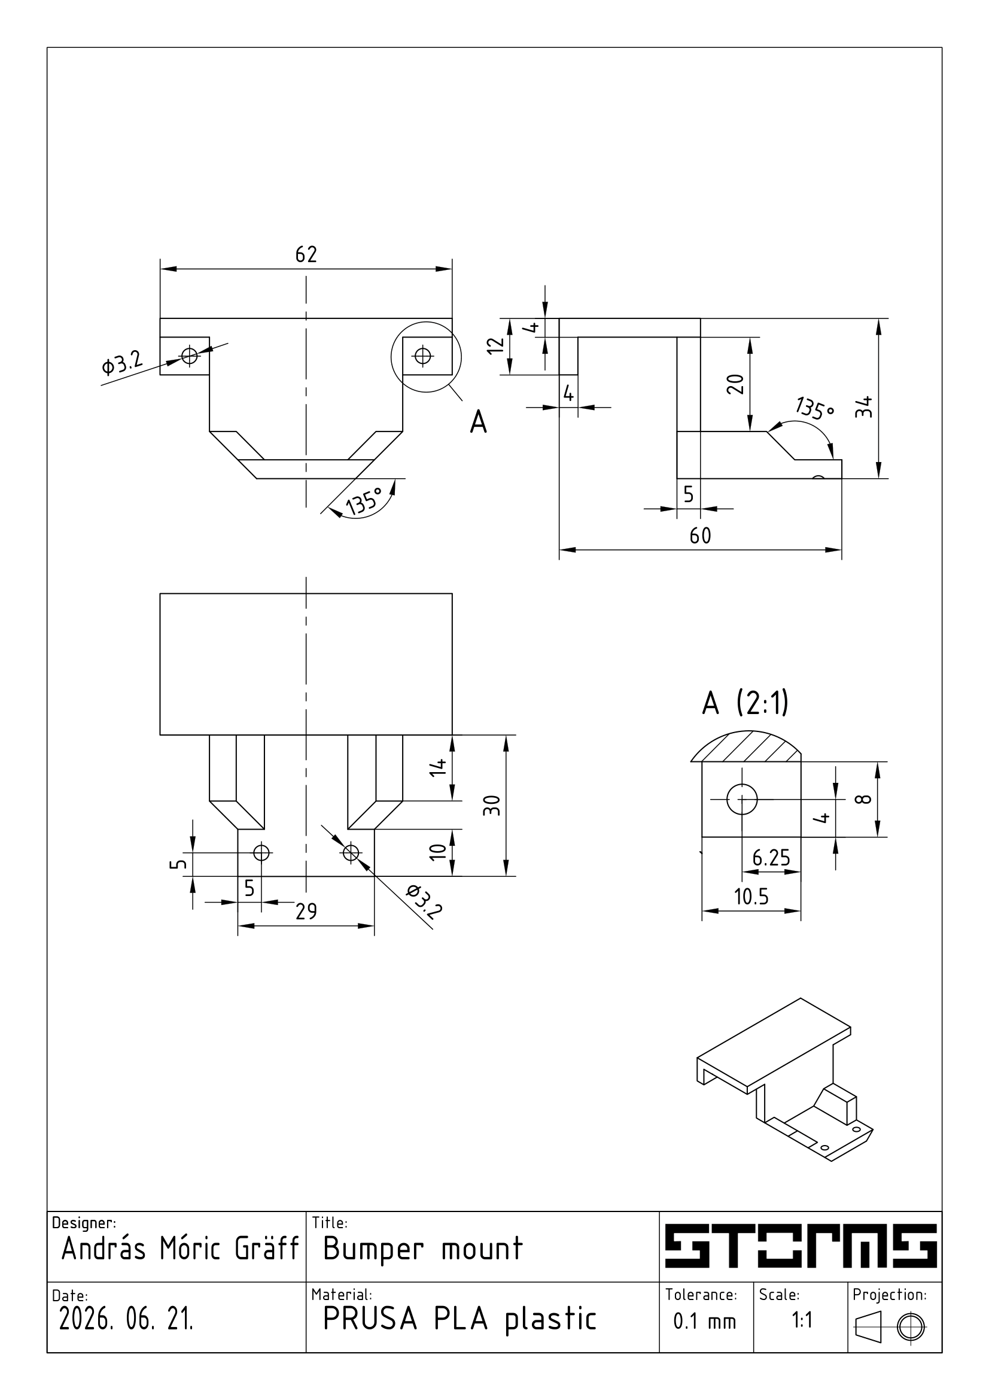
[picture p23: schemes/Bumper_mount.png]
bumper mount


This mount attaches securely to front of the robot, meanwhile allowing us to use a bumper made from a softer material, like **TPU.**

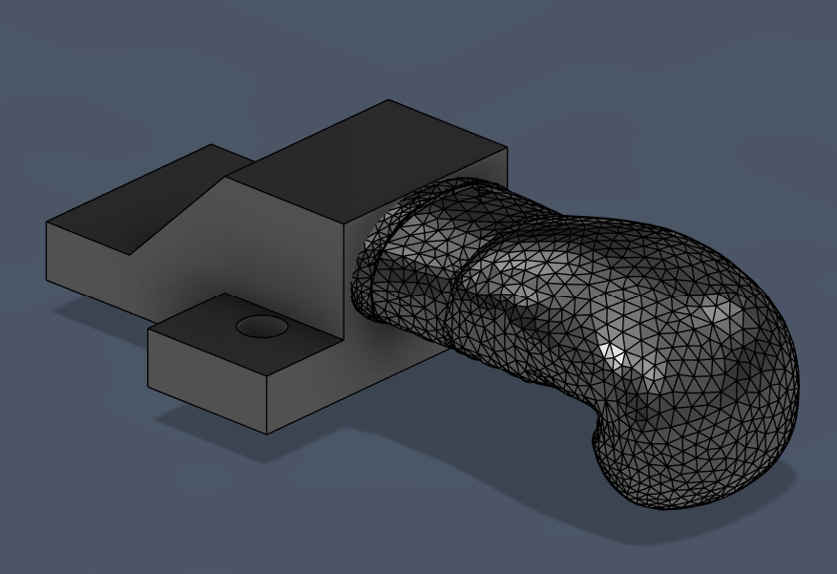
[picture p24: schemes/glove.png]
tpu bumper


This boxing glove is the bumper we landed on this year. It was printed in red TPU with an infill of only 10% to make it extra squishy. This not only improved the looks of our robot, but also made it stronger since, the **TPU could provide cushioning upon an accidental collision.
**
  license plate

  We also made a license plate. It has no function, it is just there for fun.

---

## Conclusion
  
  Designing custom 3D printed parts is hard and while sometimes we can get lucky, like with the lidar mount, **other times it may take a long time and multiple versions until we get it right.** The step by step guide was written according to the **things we learned during our process and things we will be doing in the future.** Making sure that a design is good can be one of the most important steps during the entire process of making a robot. It is of the utmost importance to ensure that **the amazing software one might have doesn't get bottlenecked by bad parts.**

# Building instructions
The 3 decks of our robots are based on the decks from the HiWonder Ackermann Intelligent Car, but you could use any material. Screwholes won't be a problem either, just note the critical measurements and drill them yourself!

First we sawed off parts of the bottom and top decks, as can be seen on this sketch:

sketch showing cut bottom deck

Then we repurposed the top deck's rear sawed off part as the third deck.

image showing the third deck

These decks can be mounted on each other with large spacers. The steering mechanism we used from the Ackermann Intelligent Car also plays a role in the structural integrity of the robot.

On the bottom deck we have the aforementioned steering mechanism, differential gearbox, the motor and the battery. How the differential gear-system is made up is detailed in the [Drive](#drive) and [The design process of 3D printed parts](#the-design-process-of-3D-printed-parts) sections. The motor has to be secured down, for this we used the original motor mounting bracket. The battery's position is not important as long as its secured down. This decks intentionally contains most of the heaviest components (the motor and the battery) in order to keep the center of gravity low.

bottom deck of the robot with all components

The middle deck contains the main computing units of the robot, the Raspberry Pi and the ESP microcontroller with the custom-made interconnect panel. It also houses the gyro and the LiDAR sensor, which has to be placed right on the front of the deck, upside down, as secured down with our custom 3D printed LiDAR bracket and ideally supplied with an at least a 230° vision free from any blocking elements. Under the Raspberry Pi is our 3D printed tunnel piece, which has to be installed in a way that both ensures backwards vision to the LiDAR, free from any interfering objects, such as loose cables, and also acts as a support for the Pi and the ESP board. The camera is also installed on this deck by 2 screws, behind the LiDAR. The buzzer can be fixed anywhere, we used a small strip of [3M Double Lock](https://www.3m.com/3M/en_US/dual-lock-reclosable-fasteners-us/) tape, so we can remove it if necessary.
middle deck of the robot with all components

The top deck is installed atop the middle deck by two screws and spacers. It's not suitable to support serious weight, but this is not a problem since the components on there are really light. It houses the motor controller, the step-down-module (PSU) and the Led&Key panel. For the PSU and the Led&Key it was important that they're installed somewhere visible since they have displays with important information, so the top deck was perfect for them. On the Led&Key there are also buttons, which we use to start the rounds, so it's really important that these are supported, since a lot of force is going to be affecting them from above(pressing). We solved this by supporting the buttons from below using spacers. The third deck has to be relatively lightweight to not raise the center of gravity too high.

top deck with all components

All components have to be installed using small spacers to avoid contact with the metal decks. Wiring between components is done using jumper cables, or in some cases thicker power cables for 12V. For more details on the wiring refer to [Wiring diagrams](#wiring-diagrams).
## Conclusion
We had quite a few difficulties during the assembly and planning process, but we are very proud of our work. If there are any problems or further questions don't hesitate to contact us at csabi@molnarnet.hu (Csaba) or andrasgraff@gmail.com (András)

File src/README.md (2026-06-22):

# Software Architecture and Obstacle Strategy

This document serves to showcase all our different software solutions, that the ESP microcontroller and the Raspberry Pi serve as the basis of.
The Pi serves as the brain of the robot while the ESP is mostly responsible for low-level tasks. The base of our code is a custom framework, which runs on both platforms, written in Python on the Pi and in C++ on the ESP. It handles communication with different sensors, sometimes even byte-by-byte packet handling. It has a lot of movement, sensing, and high-level functions. When solving the open and obstacle challenge we applied one of our core principles of simplicity and broke both challenges down to their simplest forms.

This document also includes a software setup guide, detailing what libraries and environments we used and how to install them.

## Sensors and motors

The different communication protocols and libraries used between the components of the robot and their hierarchy:

The different communication protocols used between the components of the robot and their hierarchy:

- Computer
  - Raspberry Pi `SSH` **custom VScode extension**
    - ESP `UART` **custom serial protocol**
      - IMU `UART-RVC` **Adafruit_BNO08x_RVC library**
      - Motor encoder `Digital`
      - Motor driver `PWM` 2x`Digital`
      - Servo `PWM`
      - LiDAR (control) `PWM`
    - LiDAR (receive) `UART` **custom protocol implementation**
    - Led&Key panel `Data, Strobe, Clock` **TMBoard library**
    - Buzzer `Digital`
    - Camera `FFC` **picamera library**

Communication between the Raspberry Pi and the computer is handled by our custom-made Visual Studio Code extension, RpiCode. It creates the SSH connection over WiFi or Ethernet and enables us to upload or download files and even view live sensor data. More information about the extension can be found in the [RpiCode documentation](/other/RpiCode/README.md).

We use a plethora of different sensors and motors to make the robot go. For some of the sensors we simply used pre-made libraries for communication. This is usually the best decision as most of these libraries are made by the manufacturers themselves, who have the deepest understanding of the inner workings of the sensor. In other cases we had to write some simple code where most of the logic is setting pins to `HIGH` or `LOW` or detecting when pins change state. However in multiple cases for one reason or another we had to create our own solution. One of these cases is with the LiDAR sensor, as there were no Python libraries/solutions on the internet. We studied the [official developer documentation](https://www.elecrow.com/download/product/SLD06360F/LD19_Development%20Manual_V2.3.pdf) of the sensor, specifically the byte order in the serial communication. An image of that can be seen here: image showing the byte order

Our solution was to read the incoming data byte-by-byte and store every byte in an array until a full packet is received. The start of a packet is marked by the Header byte and since the packet byte-size is fixed, we read that many bytes. After this the packet is processed all at once. The sensor sends roughly 10 packets per second by default. Most numbers are in a two byte format, so we had to shift `M`ost `S`ignificant `B`yte then add the `L`east `S`ignificant `B`yte to get the full number. This part of the code can be found in [src/RaspberryPi/LidarService.py](/src/RaspberryPi/LidarService.py).
We also had to speed up the sensor to its maximum velocity, enabling us to receive measurements up to 15 times a second instead of 10, which was necessary to keep up with the high speed movement of the robot. This was done by sending a specific `PWM` signal from the ESP at a specific frequency. This proved challenging due to poor and lackluster documentation, our solution can be found in [src/ESP/run.ino](/src/ESP/run.ino) in the setup function.
However to receive 360 degrees worth of data 15 times a second would be 5400 measurements/sec, but the LiDAR only operates at 5000 Hz. This meant we wouldn't get measurement data for every degree. We solved this by detecting "gaps" and filling them with the measurement data of neighboring degrees.

Another case where we had to create our own communication solution was between the ESP microcontroller and the Raspberry Pi. Initially we used `I2C`, but it was unreliable so we switched to serial communication. We created our own protocol for two-way communication between the two devices. Since the ESP takes care of most sensor readings and the Pi needs up-to-date information we decided on a packet-based system where the ESP sends all sensor information 100 times a second. This packet is structured like this:

| isSynced | heading | encoderLeft | encoderRight | speed | vMode | sMode | logVar | checkSum |
|---|---|---|---|---|---|---|---|---|
| 1 byte | 4 bytes | 4 bytes | 4 bytes | 4 bytes | 1 byte | 1 byte | 4 bytes | 4 bytes |
| Is the ESP synced with the Pi | IMU heading angle | -EMPTY- since we have no left motor, legacy value | Right motor encoder position | Speed of the motors in encoder ticks/second | Velocity Mode, describes the current state of the motors such as forward, braking or unregulated | Steering mode, can be IMU-controlled, arcing or free | Log variable, used for debugging | checkSum value |

### Checksum
In every packet a checksum value is included. This is calculated by taking the modulus of every field with 256, adding them together, taking the modulus of the sum +1 with 256 again. Here's what it looks like in practice:
```python
(1+ (isSynced % 256) + (heading % 256) + ... + (logVar % 256) % 256)
```
This value is also calculated by the Raspberry Pi, and if the sent value doesn't match the packet is invalidated. The extra 1 is added so a stream of 0-s isn't a valid packet. The purpose of this checksum field is to help detect and fix communications problems with a helpful side-effect of possibly saving a run, it is not the fix itself.

### Commands

Since the ESP also controls the motors the Raspberry Pi needs to be able to send commands. These commands can be sent anytime, but they also follow a structure:

| CMD | params |
|---|---|
| 1 byte command identifier value | 3 byte command parameter |

We used little-endian to determine the order of the bytes. An example command to set the target speed (command identifier bytecode `0A`) to 1000 (in hexadecimal `E8` `03`) would look like this:

| 1. | 2. | 3. | 4. |
|:---:|:---:|:---:|:---:|
| `0A` | `E8` | `03` | `00` |

We use a 'heartbeat' system between the two units. The Raspberry Pi sends a heartbeat pulse every tenth of a second, and if the ESP doesn't receive this signal it stops all motors, resets the servo and updates its `isSynced` variable. This is a failsafe in case the Raspberry program crashes while the motors are on.

All of this code can be found in [src/RaspberryPi/ESP32_Service.py](/src/RaspberryPi/ESP32_Service.py) and [src/ESP/run.ino](/src/ESP/run.ino).

For the Led&Key panel we used a preexisting Python library that enabled us to set the display and the individual LEDs or check is a button is pressed.  Using the buzzer was also really simple, we just had to set the `+` pin to **HIGH** to start the sound and to **LOW** to stop it.

For the IMU we opted to use `UART-RVC` communication protocol, where RVC stands for Robot Vacuum Cleaner, since its most commonly used to help navigate robot vacuum cleaners. We choose this mode because this was the simplest one to implement, the sensor just sends the positional data 100 times a second.

For the encoders we registered the **A** and **B** pins as interrupt pins, and counted how many times they go from **HIGH** to **LOW** or vice-versa, per second, and this would tell us the speed of the robot, with one detection being one "tick". How this translates to cm/s depends on the gear ratio of the motor, the ratio of the differential gear and of course the diameter of the wheels. In our case one centimeter equals roughly 12.4 ticks. Our maximum speed is around 3200 ticks/second which comes out to roughly 260 cm/sec, or `2.6 m/s`. During the open challenge we drive at around 2500 ticks/s or `2 m/s`, and for the more precise obstacle challenge at around 800 ticks/second, `0.65 m/s`. We go as slow as 300 ticks/s, `0.24 m/s` during parking.

Steering with the servo is achieved by sending a `PWM` signal to the servo with the correct **dutycycle**. The same is true for the DC motor through the motor controller. More information about the mentioned libraries and how to install them can be found in the [software setup guide](#software-setup-guide).

For the camera we used the native `picamera` library with the Python opencv library, `cv2` for accessing the camera feed and performing image analysis.

## The framework - basics

The Raspberry Pi and the ESP microcontroller work together, the ESP mostly completing commands sent by the Pi. The code on the ESP is running constantly, and is made up of two core components: a Main Loop and a Timer Interrupt that uses the hardware clock on the ESP microcontroller to run exactly 100 times a second. The Main Loop is responsible for reading sensors, such as the IMU sensor and doing simple calculations such as automatic continous IMU angle counting which entails detecting when the IMU angle would loop over from 360° to 0° and adding 360° to the count. It is also sending data packets to the Raspberry Pi and receiving and executing commands.
  The Timer interrupt handles speed regulation and steering, both using `PID` regulation, taking into account the current `vMode` and `sMode`. These modes define the steering and driving of the robot, both of which is controlled on the lowest level by the ESP. The Raspberry Pi only needs to send the relevant parameters over then set the `sMode` and `vMode`, and the rest is handled by the ESP. For example to drive straight the Pi needs to send over the target speed, target angle then set `vMode` to `VMODE_FORWARD`, `sMode` to `SMODE_GYRO`, so the speed and direction keeping is handled by the ESP.

To ensure accurate arcing (handled on the ESP) we had to compensate for the speed of the servo. Since our servo takes a considerate amount of time to turn from the outermost position to the center (~0.2 seconds) waiting until the target angle is reached and then turning straight is not correct, as during this ~0.2 second the robot continues turning, missing the target angle. To combat this we introduced a `predictedYaw` variable which linearly interpolates based on the past gyro measurements 0.2 seconds into the future, which we use to stop when it reaches the target angle. This, of course, is far from a perfectly simulated calculation, but we were able to calibrate the parameters for our use case with great results.

On the Pi side there are 3 important processes. There is the main thread running the challenge code. This thread is usually blocked waiting for condition, such as going *x* centimeters, or until the robot is *x* centimeters from the wall. This thread can also send commands to the ESP.

There is also a Communications process. This process is responsible for receiving data from the ESP and the LiDAR and process said data, storing it in easy to access variables and arrays. It is also responsible for sending heartbeat signals and handling Pi-side acceleration. Since multiple threads may communicate with the ESP we used a [Lock system](https://en.wikipedia.org/wiki/Lock_(computer_science)) which ensured that the two threads don't try to send commands to the ESP at the same time and end up mixing the byte order. This process also receives and processes data from the LiDAR sensor. It is really important that this thread doesn't get blocked since then we would't have up-to-date data, and the two devices might even fall out of sync. This is why we created the third process, the log thread.

This thread is responsible for writing all log data into files about 10 times a second so that later we can "rewatch" the robot run using the RpiCode tool, this is further explained in the [RpiCode documentation](/other/RpiCode/README.md). This includes log messages, current angle of the robot but also the current view of the LiDAR 10 times a second. The logs also contain every "LiDAR operation" conducted in that 1/15 second, such as checking the distance in an angle using `readLidar` or using `findNearestPoint`. We found that this many file operations can sometimes cause delay, however this thread intentionally doesn't do anything critical, in the worst case we will receive log messages a little later.

Finally, we run image analysis on a separate processor core (not thread as that can be blocked by incorrect task scheduling), so this way the resource intensive processing doesn't interfere with the regular operation of the robot and more time-sensitive operations.

## Framework - functions

We knew we wanted a really simple yet reliable framework as we found during our previous competitions in robomission that a good framework is extremely important. It can both make writing challenge code easier and trivialize implementing small rule changes each year.

The framework is made up of movement, sensing and high-level functions.

### Movement-related functions:

For movement we have an absolute-angle-system, which means that instead of turning 90° degree we turn *to* the 90° position, which will always be *right*. We have a global *tempo* variable set by `setTempo()` which provides us with an abstraction layer over the control of the robot's speed. It is detailed in the [High-level functions section](#high-level-functions).

`settargetSpeed(targetSpeed)`  
Sets the Pi-side acceleration target to `targetSpeed`. The Pi will gradually accelerate (or deccelerate) to this speed while sending over the current speed to the ESP.

`go(direction, speed_override)`  
The most important movement function, it starts the motors and tells the ESP the target direction (absolute). The speed will be the current *tempo*, unless `speed_override` is specified, in which case it goes with the parameter's value, without changing the *tempo*. After sending the commands the function returns, it's non-blocking and takes negligible time to run.

`goUnreg(force, direction)`  
Tells the ESP to start the motors with constant `force` instead of using the PID speed control algorithm, and `direction` (absolute).

`waitCM(cm)`  
Blocks execution until the robot has traveled `cm` centimeters, using the encoder data. If `cm` is negative it waits until the robot has traveled `cm` centimeters backwards.

`waitLidar(angle, cm)`  
Blocks execution until the LiDAR sensor reads a smaller value than `cm` in `angle`.

`waitAbsLidar(angle, cm)`  
Same as waitLidar except factors in the IMU sensor degree to achieve absolute angles. For example `0°` is always the front wall and `90°` is the right wall regardless of actual robot rotation.

`stop(brakeForce, wait)`  
Tells the ESP to start braking with a default braking force unless `brakeForce` (0-100) is specified. If `wait` is true it also waits until the robot is stationary before returning.

`arc(toDegree, speed_override, percent)`  
The robot arcs until it reaches `toDegree` (absolute) with the current *tempo* unless `speed_override` is specified. Percent means how much the wheels are turned during arcing. 100 means turned the maximum amount. It blocks execution until the target degree is reached, then switches to going straight and returns.

`setLane(wallDirection, targetDistance, is_small)`  
Moves the robot `targetDistance` centimeters away from the wall in the specified direction. This could mean moving closer or further away from the wall. The movement consists of going toward the wall (or away) until target cm is reached, then arcing straight. Since while arcing the robot's distance from the wall changes we have to somehow combat this. `is_small` defines the *profile* of the operation, which among other things determines the angle and the offset of the arc.

For example, completing a 1 meter square (with rounded corners) would look like this:

```python
setTempo(1000)
go(0)
waitCM(100)
arc(90)
go(90)
waitCM(100)
arc(180)
go(180)
waitCM(100)
arc(270)
go(270)
waitCM(100)
stop(wait=True)
```

### Sensing functions

`readLidar(angle)`  
Returns the distance measured by the LiDAR sensor at `angle` using the last stored measurement, in centimeters. Also handles LiDAR **deadzone** checking, since the sensor can't see all 360°, some are covered by the robot's parts. Since its mostly used to measure wall distance this function can return so-called *phantom distances*. This means that instead of returning the faulty deadzone distance we measure the closest non-deadzone distance and using trigonometry calculate the distance for the original degree by assuming we are measuring the distance along a wall (so perpendicular to it):
illustration showing phantom distances
The area between the gray lines is the zone where the LiDAR is blocked, the dotted red line is where we want to measure (perpendicular to the wall) and the solid red line is the first non-deadzone angle where we can measure distance. Alpha is the difference between the measuring angle and the requested angle. By imagining the right triangle defined by $\alpha$, measured distance and phantom distance we can calculate the unknown length of phantom distance:

$$\text{phantomdistance}=\cos(\alpha)\cdot \text{measureddistance}$$

`readAbsLidar(angle)`  
Same as `readLidar` except it uses the IMU angle to calculate in absolute angles (the front wall is 0°, the wall to the right is 90° and so on).

`findNearestPoint(bottomLeftX, bottomLeftY, topRightX, topRightY)`  
Uses the LiDAR sensor to find the nearest detected object in the specified rectangle. The input coordinates are relative to the centre of the LiDAR. First, the rectangle's corner's `x`,`y` coordinates are mapped to a Polar coordinate system (to radius and angle from the origin). After this it checks the relevant angles, which are the angles between the bottom left corner's Polar angles and the top right corner's Polar angles. Then at all the relevant angles the angle and the LiDAR measurement (angle and radius) is converted back into `x` and `y` coordinates, relative to the center of the LiDAR sensor. After that, it checks if the converted point (x and y coordinate) is inside the rectangle defined by the parameters. If it is, then it gets stored. Finally it returns the closest stored point, which is the one with the lowest `y` value (relative to the center of the LiDAR). This function has two really important use cases. It can either be used, as the name implies, to find the nearest point and get its x and y coordinates relative to the robot. This could be used to decide the position of traffic signs for example, but for this we rather use the later detailed `findNearestObj`. The other use case is to simply check if there is an object in the selected rectangle or not, since if no objects were found it returns `-1`. This is the main use case, for example to check the driving direction during Open Challenge by looking for a "gap".
This use case visualized in our [custom sensor data visualizer](/other/RpiCode/README.md):  

  (The white points are all what the LiDAR sees, the white lines are the "angles of interest", the red rectangles are where its checking for objects)

`findNearestPointAbs(bottomLeftX, bottomLeftY, topRightX, topRightY)`  
Same as `findNearestPoint` except it uses the bottom left corner of the current section on the mat as the origin point for the given coordinates (`bottomLeftX`, `bottomLeftY`,...) by measuring the distance to the left wall and to the back wall. If an object was found the detected point is returned also relative to the bottom left corner.

`findNearestObj(bottomLeftX, bottomLeftY, topRightX, topRightY)`  
Works similarly to `findNearestPoint` except it detects the start and end point of an obstacle (in our case a traffic sign). This data is represented by a `dataclass` with some key variables (starting point, endpoint) and some convenience methods such as calculating the centre of the object or checking whether the object was found or is `empty`. This data is crucial for detecting the color of the object.

`findNearestObjAbs(bottomLeftX, bottomLeftY, topRightX, topRightY)`  
Same as `findNearestObj` except it uses the gyro and the LiDAR to calculate the position relative to the bottom left corner of the current section, similarly to `findNearestPointAbs`.

`mapPointToCam(pointX, pointY, pointZ)`  
This function converts a point in 3D space, relative to the projection of the centre of the LiDAR on the mat to a pixel coordinate. After much thought we were able to reduce the problem to **two trigonometric functions**. First we calculate the X,Y,Z distance of the camera and the point using the known position of the camera. After this imagine the point of the camera and the given point viewed from above, and draw in the imaginary right triangle like so:illustration showing said triangle  (X axis is sideways, Y axis is forward, example is detecting the top right point of a green traffic sign's front face)

Now do the same but viewed from the side:
Illustration showing said triangle
(Z axis is up, Y axis is forward, example is detecting the top right point of a green traffic sign's front face)

Using the known distances we can calculate α and β, which specify how many degrees the point is away from the centre of the camera horizontally and vertically. After measuring the `FOV` of the camera, assuming a linear relation between degrees and pixels (the image is not distorted) and factoring in the vertical (and possible horizontal) rotation of the camera we can calculate the pixel location of the object on the camera image:

$$x = \frac{640\text{ px}}{53^\circ}\cdot \arctan\left(\frac{Z_{\text{difference}}}{Y_{\text{difference}}}\right)$$
$$y = \frac{480\text{ px}}{41.5^\circ}\cdot \left(\arctan\left(\frac{X_{\text{difference}}}{Y_{\text{difference}}}\right) + 15^\circ\right)$$

(The image is 640px*480px, horizontal FOV is 53°, vertical FOV is 41.5°, horizontal rotation is 0°, vertical rotation is 15°)

`detectObjectColor(Object obj)`  
Detects the color of the object by first calculating the pixel location of the top left point of the traffic sign and the bottom right point of the traffic sign gathered from the `Object` dataclass parameter. Then utilizing multiprocessing uses `cv2.mean` to calculate the average of the selected area, plus we add a safety border of around 5 pixels. Finally we subtract the `green` value from the `red` value, and compares this number to a well-calibrated border value to determine whether the sign is red or green.

### High-level functions

These functions are more complex, mostly made up of other framework functions.

`initLoop()`  
Always called at the start of the program, initializes some variables, establishes connection with the ESP and other sensors, starts all processes and waits until the first button on the LedAndKey panel is pressed, after which it returns, and the robot run can start. While the button is not pressed it uses the LedAndKey's display to show useful debug sensor data. With the press of the second button you can cycle between different displays. The LEDs also display useful diagnostics information.

`setTempo(newTempo)`  
Sets the *tempo* global variable alongside setting the current `targetSpeed`. We like to think of this like a speed limit sign as we can insert this before critical parts of the mission, like adding it to `turnCorner` to make every turn precise, or before switching lanes. Except instead of being a speed **limit** it specifies the target speed, it can also be inserted in the strategy to speed up the robot in long straight sections for example.

`calcLaneFromObs(column, color, wide_avoid)`  
Calculates to which lane the robot has to switch to in order to avoid the traffic sign in the given `column` and `color`. If color is red is returns the next lane to the right of the lane of the sign, and if it's green then the one to the left of it. One example:  
showing the robot's choice  
Here the robot detects a red traffic sign in the left column and chooses the lane to the right of it. More details about the lanes in the strategy section.  
If `wide_avoid` is true it only returns the left lane or the right lane, thereby sometimes travelling extra distance. In the example above it would return the 40 cm wide section The parameter was added to make the surprise rule and future suprise rules easier to implement.

`switchLane(newLane)`  
Switches lanes to `newLane`, which is a constant specifying one of the *lanes* the robot can operate in. More on this in the strategy. After making some calculations, such as determining whether it will be a small distance or a long distance from `lane` and `newLane` and setting the `is_small` parameter accordingly, it calls `setLane` with the correct parameters.

`correctWallDist(walldirection, targetDistance)`  
Works similarly to `setLane` but moves at a very limited angle (10°) so arcing straight at the end won't affect the distance from the wall, enabling extra precise positioning. Designed for when the robot has to move straight for an entire section, so it has a lot of space for precise movements.

`waitEnsureDist(target_dist, allowed_deviation)`  
Ensures the robot is `target_dist` away from the front wall by backing up if the it's too close. `allowed_deviation` serves as a buffer, if the robot is only off by this much then no backing up is performed. This is useful when for example we want to turn around the corner at a specific point to end up in a specific lane. This way `allowed_deviation` can be used as leeway to avoid the time-intensive backing up manouver. The distance is always measured from the front wall by `readAbsLidar(0)`. 

`findFirstObsInNextSection()`  
Finds and returns the first traffic sign in the next section before the corner turn using `findNearestObjAbs()`. Does so by first detecting traffic signs in the first and second row (there can be only one), and if none was found then in the third row.  
showing use

`turnCorner(targetLane, detection_careful)`  
Turns the corner at the and of a section. Is `detection_careful` is false then it performs a single arc at the correct distance away from the front wall to end up in the specified `targetLane` (which is one of the *lanes* the robot can operate in). If `detection_careful` is true it instead completes a turning manouver depending on the current *lane* of the robot which will end up backed near the backwall facing the first obstacles of the next section. More about the turning manouvers in the Strategy section.

`getFirstTurnTarget()`  
Calculated to which lane the robot needs to turn to during the optimized laps. Similar to `calcLaneFromObs()` except it performs one additional path optimization. If there are two signs of the same color in different columns we make sure to target the *inner* or the *outer* lane, prohibiting optimizing by moving to the *obstacle lanes* to avoid having to do a `switchlane` between the two.  
showing the optimization in work
(Illustration showing the additional path optimization in action as the green arrow and the red arrow is without optimization)
## Robot run strategy

### Open challenge

In the open challenge the robot first determines the driving direction, then goes to the outer lane and completes 3 laps while staying on the outer lane the whole time, accelerating and decelerating to lower lap times but maintain precision where it counts.

The strategy of the placement of the robot inside the selected starting zone by us is the following:

image showing all starting positions

We try to have the robot near the center of the lane vertically, and somewhere in the middle horizontally.

At the start of the round the robot has to recognize the driving direction. This is done in multiple steps. First, the robot checks if it is directly next to a wall using the LiDAR sensor. This is only possible if the starting zone is one of the middle ones and the wall is on the outer position in the starting section, as can be seen on the previous illustration. If it is next to a wall that determines the driving direction for certain. If the wall is to the left of the robot then it will have to turn left at the corners and if it's to the right, then right. If a close wall was detected the robot will first move to the center of the available space by going at a 45° angle until the distance to the outer wall is half the available space (30 centimeters), then continue the round as normal.

An illustration showcasing direction detection:

illustartion

```python
if close wall detected:
  if close wall is to the left then:
    driving direction = counter-clockwise
    go at angle 45°
  if close wall is to the right then:
    driving direction = clockwise
    go at angle -45°
  wait until distance from outer wall is 30 cm
  go at angle 0°
  
```

If there are no close walls the robot will decide the driving direction using the LiDAR. To make the measurements reliable it first goes forward, and then using the powerful `findNearestPointAbs` function checks which direction the open space is, and from this determines the driving direction.

After this both cases join, and the robot enters a simple loop which consists of going straight and arc-ing in the right, previously decided direction in the corners. The robot goes forward until the distance from the front wall is so a 90° arc will end in the next straight section's outer lane. To maximize the speed of the robot while keeping the corner turns precise the robot accelerates in the beginning of the straight sections and decelerates before taking the turn. Since the robot only drives in the outer lane the walls' randomization is effectively ignored, therefore reducing the possible scenarios we have to test, enabling us to test these few scenarios more, and in turn increases the run's constancy. After every turn we set an angle offset variable so that "forward" will always be 0°, this way the 4 straight sections and turns are exactly the same. This can be seen in the following pseudo-code segment:

```python
repeat 12 times:
  go
  wait until distance from front wall is 55 cm
  arc 90°
```

Finally after completing 3 laps the robot stops in the middle of the starting section.

```python
wait until distance from front wall is 150 cm
stop
```

### Obstacle challenge

In the obstacle challenge the robot completes straight sections independently of each other, going around traffic signs and avoiding the parking space. First it parks out, detects the driving direction similar to Open challenge, then in the first lap checks the color and position of the traffic signs. After the first lap it follows an opimized path. Finally after 3 laps it returns to the starting zone with the parking space, after which it parallel parks.

Simplification was our main principle when solving the obstacle challenge. This year's strategy for the national finals is a compromise between the simple and reliable strategy used at the 2025 international championship and an optimized fast strategy we came up with. After implementing parts of the optimized strategy we realized it would be far too complex and hard to test and make sure its reliable, so we came up with this. This strategy massively speeds up the detection lap, while also keeping the simplicity of the old strategy. More about how and why we made this choice in the [Our Journey document](/Our_Journey.md).

First, we broke down the mat into 4 independsent **sectors**, each consisting of 1 straighforward section and 1 corner section. We also broke down the straightforward sections into 4 **lanes**, areas the robot can operate in.
#### Keywords
A short summary of the different keywords we will be using throughout the strategy documentation.
- **Section**: One of the 8 1 meter x 1 meter areas.
- **Straightforward section**: One of the 4 sections where the robot has to drive forward and avoid traffic signs.
- **Corner section**: One of the 4 sections with the orange and blue lines. Here the robot has to turn 90° to continue the on the field.
- **Sector**: Our own definition, consists of a corner section and a neighboring straightforward section in this order. There are 4 sectors on the mat.
- **Row** (straightforward section): On the Straightforward section there are 3 rows, in each of them are two possible traffic sign locations. They're numbered from 1-3, starting with the one the robot would first encounter with the current driving direction.
- **Column** (straightforward section): The dotted lines on the straightforward sections, each containing 3 possible traffic sign locations. They are named relative to the driving direction.  
rows 1-3 and columns right and left  Illustrations showing the rows' and columns' position. The values in the parentheses is how we refer to them internally in the code.
- **lane**: Our own definition, specific walldistances in the straightforward sections where the robot can operate. We have 4 lanes. The two 40 cm wide areas and the dotted lines (columns) are considered lanes. The latter are also referred to as *obstacle lanes*, but they are full value-fledged lanes.  
4 lanes  
Here these lanes are illustarted as a wide rectangle, but in reality they are 1 specific walldistance, a line. Of course the movement of the robot isn't perfect, so it's rarely at the exact distance, but we try to minimize the offset to at max 10 cm. This is what we use `correctWallDist()` for.  
We mainly refer to these lanes relative to the driving direction (left, right...), but sometimes we need to refer to them relative to the walls of the field (inner, outer...). The distance between two neighboring lanes is 20 cm. The value in the parentheses is how we refer to them internally in the code.

Our goal was to make only a handful of possible driving scenarios on the straightforward and corner sections, and make them completely independent of each other. This vastly reduces the different cases we have to test.
#### Leaving the parking space
Start of the round the robot has to leave the parking space. This is a very precise operation so to eliminate slippage the robot moves at a **very** slow speed. Thankfully the robot can leave the parking space in one continuous arc. However, depending on the traffic sign in front of the robot and the driving direction there are still 4 scenarios.  If the driving direction is counter-clockwise, the robot first arcs out so the traffic sign on the third row can be detected. Then the obstacle is avoided according to its color:
scenarios showing parking out with driving direction counter-closkwise
(If there is no traffic sign we treat it as if there were a red traffic sign)

If the driving direction is clockwise, then the robot will have to avoid the traffic sign on the middle row *or* the one on the last row. The robot moves into a position where it can detect the color of potential traffic signs on the second *and* third row. After this it avoids it according to its color:
scenarios showing parking out with driving direction clockwise
(There can only be one traffic sign, either in the second or third row. There can also be no traffic sign there, which we treat as if a red traffic sign were there.)

After this the execution is passed to the detection lap loop, the robot is considered to have finished the first **sector**.
#### Detection lap
In this lap the robot has to detect the colors of all the obstacles (minus potentially the first one already detected during the parking out), and store them. We have a two-dimensional array with 4 sub-arrays for the 4 sections and in each sub-array 3 fields for the 3 rows. We call this the `trafficSignMatrix`. Each obstacle is stored as a number with a sign (-/+). The sign represents the column (-: left, +: right) and the number the color (1:GREEN, 2:RED). 0 is the default value, it means there isn't a sign on this row. So for example a red sign on the left row would be represented by `-2`.

Each **sector** is comprised of a corner segment and a straight segment, in this order. Before the turn the robot scans the next section using `findFirstObsInNextSection`. Then it performs a corner turn depending on the detected obstacle's position. There are 2 cases, depending on whether the first traffic sign is in the first row or not.

If it isn't, then the robot can perform a single arc at a calculated distance from the front wall in order to end up right in front of the detected sign, regardless of the current lane of the robot.

ahowcasing all turns

The obstacle in the 2nd and 3rd row are treated the same, the only difference is for the 3rd row we move a bit closer before taking a photo. After detecting the sing's color we perform a lane switch to the lane calculated by `calcLaneFromObs`. Since we are facing the sign we at most have to switch over 1 lane, ensuring the switch can be finished before the end of this sector, in the straight section. 

If the first sign is in the 1st row then the robot sadly can't always turn in to face the obstacle. Even when it could (coming from the outer lane) after detecting it and completing a `switchLane` there may be a seconds sign on the third row. We found the robot can't always complete two switchlanes when starting from in front of the first sign. For this reason, and to keep the flow of the program simpler if there is a sign on the first row we always perform a turning manouver which ends with the robot backed up to the backwall and facing the first sign. This does cost considerably more time, but keeping the number of cases to a minimum and keeping sections completely independent of eachother is worth it in our opinion. There are 4 lanes the robot could be coming from but only really two manouvers, as the *inner* and *inner obstacle* lanes and the *outer* and *outer obstacle* lanes are treated as the same with minor differences. Each manouver has two versions depending on where it has to end up (facing one of the columns), but the only difference is where the robot starts the manouver.  The manouvers from all lanes, with the inner and outer lanes targeting the inner column and the obstacle lanes targeting the outer column:

turning scenario turning scenario

The inner lanes' manouver is a simple backwards arc, only difference being that in the inner lane the robot moves a bit outer to avoid hitting the (possible) first traffic sign of the next row. The outer lanes' manouvers are identical, to avoid hitting the (potential) signs in the first row the first arc is incomplete (70°), the robot straightens itself while backing up. After each turn we set an angle offset variable, same way as in Open Challenge, to ensure front is always 0°, right is 90° and so on.

After completing the turn the robot detects the color of the traffic sign in front of it and switches to the lane calculated by `calcLaneFromObs()`. Then it checks if there is a sign on the third row. If there isn't one, the robot speeds up by upping the *tempo* and performs a `correctWallDistance`. The speed up is due to the robot moving straight for a long distance, and the correcttion is to correct the position of the robot in the middle of the section. If it's gyro is off by even a few degrees this adds up over 1 meter. If there is one in the htird row then it detects it's color and switches lanes accordingly, finishing the section.

As the result of the many simplifications we made to the challenge, only a handful of operations need to be fine-tuned and tested: The two backing-up-turn manouvers, the one-arc-turns' distances to start the arc and `switchlane` needs to work correctly for 20-40-60 cm wide lane switches.

After completing the first lap we no longer have to detect the color of the obstacles, which leaves the door open for further optimizations.

detection lap  
(Illustration showing a full detection lap starting from START. The red arrows represent backing up)

Pseudo code of the detection laps:
```C
repeat 4 times:
  #at the end of a straight section, before turncorner
  findFirstObsInNextSection()
  if detected obstacle is in first row:
    turnCorner(detected obstacle's lane, detection_careful=True)
    detectObjectColor()
    switchlane(calcLaneFromObs(column, color))
    if obstacle detected in 3rd row:
      detectObjectColor()
      switchLane(calcLaneFromObs(column, color))
    else:
      correctWallDist(closer_wall) //Looking at the closer wall
  else:
    turnCorner(detected obstacle's lane, detection_careful=False)
    detectObjectColor()
    switchlane(calcLaneFromObs(column, color))
```
(Many parameters are left out and variables are treated as-is, the code mainly serves to illustrate how we actually coded the challenge code in Python)

Flowchart of the detection sectors:  
flowchart of detection sectors

#### Connecting the loops
From an abstract point-of-view our code consists of a detection loop doing 1 lap and an optimized loop doing 2 laps. However in reality we already potentially detected a traffic sign during parking out. For this reason we have a special, inbetween sector we call *early-detect*. This sector combines elements of both loops. It checks whether there is a previously not seen sign and if yes detects it just like it would in the detection loop. There is at most 1 undetected obstacle, because we already checked 1 or 2 locations during parking out. After detecting the sign (or not if there wasn't an undetected one) it continues on like an optimized section.

#### Optmized laps

After all obstacles have been detected, the robot follows a much more optimized path. Most of the optimization comes from always knowing where to turn in the corner. After turning it may have to perform one more switchlane to finish the section.

The robot is able to complete the turn from one lane to another in one continous arc, a massive improvement from the detection laps' complex manouvers. Since the robot already knows the color of all obstacles, it can make one of the following turns based on it's current lane and the target lane, calculated by `getFirstTurnTarget()`:  
all one-arc turns  
As it's visible here this results in a ton of different turns, but really the only difference is a number telling the robot when to start the arc, so the incoming lane doesn't matter, we only have to fine-tune 4 values. 

Although the robot is able to complete these turns in one arc, sometimes previous delays stack up, and it might already be over it's target position. This is combatted by `waitEnsureDist()`, which backs up if too close. This perfectly ensures the previous sector(s)' delays won't effect the current sector's, at the price of a time-intensive backup manouver.

Turn correction illustrated

We only have to do a switchlane if there are two different colored traffic signs in the section. Even though there could be two of signs of the same color we optimize our path to turn in to the lane which satisfies both signs, as described in the framework documentation under `getFirstTurnTarget()`, eliminating the need for a mid-section switchlane in this case. If we do need to switch lanes we switch to the optimal lane calculated by `calcLaneFromObs()`, finishing the sector.

Here's what an optimized lap might look like, showcasing many different optimizations:  
optimized lap

With these optimizations we were able to shave down about 70 seconds from our run time, without sacrificing simplicity or reliability.

Pseudo-code of the optimzed laps:

```python
repeat 4*2 times:
  #at the end of a straight segment, before turncorner
  turncorner(according to the color of the 1st (and potentially 2nd) traffic sign in the next section)
  if(there are two traffic signs in this section and they are of different color):
    switchlane
  else:
    correcttWallDist
```

Flochart of the optmized sectors:  
optimized flowchart
#### Parking

After completing 3 laps, just before entering the starting sector the robot starts the parking procedure. We again strived for simplicity and decided to develop **one** parking maneuver and fine tune it. If there is a traffic sign on the first row of the section it still has to avoid it in the correct direction. If according to the color the robot has to move to the outer lane, or there is no traffic sign there then the robot completes parking like so:
illustration showing unified parking
The robot comes from either the right or the left, depending on the driving direction, this is represented by the black arrows. Red arrows mean driving backwards, green means forwards. Accuracy is key during the maneuver so the robot moves very slowly and constantly senses its surroundings.
  However if the sign requires the robot to move in the inner lane we can't complete this unified parking maneuver. To make it work we have to avoid the sign by moving to the inner lane. Then we switch to the inner lane, and back up (making sure we don't pass the traffic sign in the wrong direction):
illustration showing said maneuver
 After this we assume the unified parking position and complete parallel parking regularly.

### Suprise rule
For the first time in Future Engineers history there was a surprise rule announced a few weeks before the national finals, for both the Open and Obstacle challenges.

For the open challenge the surprise rule stated that ending touching the inner wall ends the run, similarly to how touching the outer walls end the run in the base rules.

In the obstacle challenge after the randomization you had to replace one of the obstacle, with the exception of the first and last sign, with a LEGO minifigure. This minifigure would be placed near the inner wall inside the green square. Touching, moving this minifigure would end the run instantly, similarly as if you avoided a sign on the wrong side or touched parking walls. Which way you avoid the minifigure does not matter.

Before modifying the code we uploaded it to GitHub and made sure to mark every changed line for the suprise rule to make reverting to the base challenge simple.
#### Open challenge solution
For this challenge the change was minimal, and it didn't effect us at all, since our strategy was already to drive on the outer lane of the mat. But since the time of the Open Challenge run is super unlikely to matter we are prepared to slow down the robot if there is any uncertainty in the run.
#### Obstacle challenge solution
First we tested if the robot can detect the LEGO minifigure. It couldn't reliably. This meant we had to plan for both detecting and not detecting the mini. If we detect it there is no problem. The robot will simply treat it as a traffic sign, take a photo and assign it whatever color it happens to detect. It will always avoid it.

If it doesn't detect it (majority of cases) we have to keep in mind that the mini has to be at a valid traffic sign spot. So we just treat every valid traffic sign spot as being occupied, even if the LiDAR didn't find anything there.  
showing possible mini locations  
(Illustration showing detectable obstacles and where the minifugre could be.)

During the detection if we detect a sign in the middle row we know that section is safe, nothing is changed.

If we detected a sign in the 1st row we do what we normally would, with the important change that we can only switch to the outer or the inner lane. The robot can't end up in one of the *obstacle lanes* to avoid hitting the minifigure, so we set `wide_avoid` to **true** in the `switchlane`.  
surprise rule illustration  
(The green arrow is the path the robot would take if the sign's color is green, the red is if it's red, the X-s mark the avoided lane)

If we detected a sign in the 3rd row we can't know the mini isn't in the 1st row so we have to avoid it by performing the turn as if there was a sign in the 1st row. Then we override the detection of the color for he nonexistent sign with an arbitrarily chosen color. We chose the color that takes us to the right lane if the sign on the 3rd row's in the right column and vice-versa, also setting `wide_avoid` to true. After that we detect and avoid the sign as we would normally in a 2 sign section.  
sign on third row  
(We avoid the potential minifigure from the right because the detected sign is in the right column)

The surprise rule also introduces a special case that we haven't dealt with before, a seemingly empty section. Previously this meant something went wrong but now this is a valid state. In this case we just move to the outer lane to avoid the minifigure.  
no obstacles detected  

Since the surprise rule stated that the minifigure can't be in the starting segment the *early detect* (section between detection and optimized loops) code did not have to be changed.

We also realized we don't have to change the optimized laps at all, if we fill out the `trafficSignMatrix` (2 dimansional array conatining detected signs) to avoid every potential minifigure position.  
If the section contains a middle sign or 2 signs nothing had to be changed, the minifigure can't be in this section. If it contains 1 sign in the 1st or 3rd row we have to make sure it doesn't optimze it's movement through an *obstacle lane* and hit the minifigure. If it's in the 1st row then we have to make sure it doesn't switch lanes into the *obstacle lane* next to the traffic sign. This can happen for example if we had detected a red sign on the left lane, in this case the robot would switch to the *right obstacle lane*. We can combat this by creating a fake traffic sign in the 3rd row with the same color but in the other column. In the strategy we specifically optimize the run by checking if there are 2 obstacles of the same color and if yes then turning straight into the lane that avoids both of them to avoid making an extra lane switch. We do something similar if one sign was detected in the 3rd row, but we create the fake traffic sign in the 1st row. There is also the case of the empty section. Here we create two obstacles of the arbirarily chosen color and place them on the 1st and 3rd rows, on different columns. An illustration showing a randomization and where the fake traffic signs were created:  
fake obstacles outlined  
(The fake obstacles are outlined with purple, the black arrows show the path of the optimized laps, the black figures show the possible positions of the LEGO minifigure)

Initially we also had an idea to simply forbid the robot from ever going to the *obstacle lanes*. The main timeloss of the optimized laps is situations where we have to backup at the end of a section because the robot finishes the section too late. This happens around sections with 2 different colored signs, and by keeping these optimized we avoid losing a lot of time compared to the simpler solution of just diabling the *obstacle lanes*.

## Software setup guide

This document serves as a guide for installing the necessary software and setting up environments on the programming computer, [Raspberry Pi 5](https://www.raspberrypi.com/products/raspberry-pi-5/) and [NodeMCU-32S](https://docs.ai-thinker.com/_media/esp32/docs/nodemcu-32s_product_specification.pdf) device. We tried to be as precise as possible when describing the steps, however if we did miss something let us know and we will try our best to help solve any problems. You can contact us at csabi@molnarnet.hu (Csaba) or andrasgraff@gmail.com (András).

### Programming computer

This can be either a laptop or a PC. We tested everything on a laptop running Windows 10, and one running Windows 11.

#### Python code editor

We used Visual Studio Code, but theoretically any code editor works. However we **strongly** recommend VScode, since the upcoming steps will be VScode-specific.
First you have to install [VScode](https://code.visualstudio.com/download). You will also need to download [Python 3.12](https://www.python.org/downloads/release/python-3120/). To connect the two finally you need to install the [Python extension](https://marketplace.visualstudio.com/items?itemName=ms-Python.Python) for VScode. Another extension we recommend downloading is [PyLance](https://marketplace.visualstudio.com/items?itemName=ms-python.vscode-pylance) which enables autocorrect for Python. To be able to download files to the Raspberry Pi you also need to install our custom-made extension **RpiCode**. This extension does way more than just upload files, for the installation process and full list of features, go to the **[other/RpiCode](/other/RpiCode/)** folder. Some libraries are Raspberry Pi **native**, so they aren't installed on the computer, the only nuisance this causes is the lack of autocomplete for those specific libraries. We simply chose to ignore this, however if you find autocomplete important you could "emulate" a library by creating a blank **.py** file with the function and class names of the missing native library, or look up how to install said library on windows.

#### Arduino IDE

The [Arduino Integrated Development Environment](https://www.arduino.cc/en/software) was our choice of software to develop on the **NodeMCU-32S** microcontroller. It's originally made for arduino microcontrollers, however it being **open source** allows manufacturers to develop custom board managers for their own microcontrollers. This is also the case with the NodeMCU-32S which is an **ESP32** microcontroller, so you will need to install the ESP boardmanager. For this we followed this tutorial ([https://www.aranacorp.com/en/programming-an-esp32-nodemcu-with-the-arduino-ide/](https://www.aranacorp.com/en/programming-an-esp32-nodemcu-with-the-arduino-ide/)). Now just make sure the attached libraries in the [src/ESP/libraries](ESP/libraries/) folder are next to the **run.ino** file in a libraries folder.

### Raspberry Pi 5

#### Setup

The Raspberry Pi 5 should have Raspberry Pi OS 64 bit downloaded. You need to create a folder that will be the destination of the file upload for the [RpiCode Extension](/other/RpiCode/README.md). You will need to install a few Python libraries using the **`pip`** tool. Pip most likely got installed along with Python but just in case it can be downloaded here: [https://pip.pypa.io/en/stable/installation/](https://pip.pypa.io/en/stable/installation/).

#### Installing libraries

- `pip install rpi-lgpio`
  - **GPIO** pin manager library for Raspberry Pi 5
- `pip install serial`
  - **Serial** communication library
- `pip install rpi-TM1638`
  - [TMBoard](https://thilaire.github.io/missionBoard/TM163x/) panel library
- `pip install picamera`
  - **Camera** module
- `pip install opencv-python`
  - **OpenCV 2** Python library
  
If you successfully install the libraries but still receive a module not found error try replacing the `pip` keyword with `pip3` or `pip3.12`.

There are some other libraries that don't need to be installed using `pip` because the source file is attached in the [src/RaspberryPi](RaspberryPi/) folder.

For the upload function of the extension to work the computer needs to be on the same WiFi as the Raspberry Pi. This can be achieved many different ways, we opted to use the Pi as a host and connect with the computer to the hotspot. Following the [official documentation](https://www.raspberrypi.com/documentation/computers/configuration.html#enable-hotspot) you have to type the following command into the terminal to start a hotspot:

`sudo nmcli device wifi hotspot ssid <example-network-name> password <example-password>`

To automatically start the hotspot every time the Pi boots up, you can append the command to the `rc.local` file which you can edit by typing `sudo nano /etc/rc.local` into the terminal.

The final thing to do is to enable program start on **boot**. This can be done in many different ways, here's a tutorial ([https://www.dexterindustries.com/howto/run-a-program-on-your-raspberry-pi-at-startup/](https://www.dexterindustries.com/howto/run-a-program-on-your-raspberry-pi-at-startup/)) we followed that explains 5 different methods.

### NodeMCU-32S

#### Connect

The microcontroller needs to be **connected** to the computer via a micro USB cable, or a USB-C cable if you're using a newer model. If you followed the previously linked [NodeMCU tutorial](https://www.aranacorp.com/en/programming-an-esp32-nodemcu-with-the-arduino-ide/) correctly and after plugging the device in this message should appear in the bottom right corner:  NodeMCU-32S on COM5
If this is the case then just pressing the **upload** button should start the code.

# Contact

If you have any further questions feel free to contact us at csabi@molnarnet.hu (Csaba) or andrasgraff@gmail.com (András).

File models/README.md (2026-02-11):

This folder contains the various 3D printing files. The design process and usage of these parts are documented int the [Hardware documentation](/schemes/README.md#the-design-process-of-3d-printed-parts).

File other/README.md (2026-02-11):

# RpiCode installation and features guide

In this guide I will talk about our VSCode extension RpiCode, how to install it, set it up, and what kind of features it provides. **This extension is still heavily work in progress,** however the feature it does already have are in a usable enough state to use it daily.

RpiCode is both a development tool as a file manager and remote program runner for the Raspberry Pi, and a sensor-data visualizer which combines the LiDAR data with the IMU angle and the camera data alongside a log message replay. Producing a nice and useful visualization of the entire robot run, live, or from the downloaded logs, while being integrated into VScode in the form of an extension. The logs are created by our custom sensor & messages logging library which we have integrated into the robot run's code.

---

## Installation

### Installing the extension

**Download the `rpicode.vsix` and then open vscode.** In vscode select a workspace folder by clicking on the explorer icon on the left and clicking open folder.

Open folder

**Make sure that the file is in that folder.**
After that make a new terminal by clicking the three dots on the top next to `Go` , selecting `Terminal`, then `New Terminal`. In the terminal type the following command:

> code --install-extension rpicode.vsix

In case you change the downloaded files name, **change rpicode in the command to the new filename.**

### Installing the required python libraries

In this step I'm going to assume that python and pip have already been downloaded, **however if not, then visit our software [installation guide](/src/)**.

In the terminal type the following commands:
> pip install PyQt6

 Installs PyQt6 graphical interface library

> pip install Paramiko

 Installs Paramiko ssh library

> pip install websockets
 
 Install websockets websocket library

## Setting up the extension

After the installation is done, go into the extension tab on the left, then select rpicode, find the cogwheel and click extension settings. **There you can find all the settings with descriptions**. I should add however that the ip section doesn't necessarily need to be filled out, since by default it uses `raspberrypi` instead which works, most of the time. **Will probably not work and the ip will be needed if multiple raspberry devices are on the same network.**
If everything is done correctly then the extension should start on startup.

settings

---

## Features

- ### The Terminal
  After successfully starting the extension a button called `Create connection` Create should appear **on the status bar at the bottom right.** Before pressing it make sure once again that the **settings are filled out correctly and you're on the same internet connection as your device,** but an ethernet can be used as well. After pressing it a new terminal by the name of `run` is created. Wait a bit until you you see the following text: `cc>`. The terminal has 3 modes:
  - Custom command:
    It is the default mode, but can be accessed anytime by typing `cc`. It only has a few **commands which can be checked by typing `help`.** (The command `diagno` does nothing at the moment)
  - ssh:
    This mode can be chosen by typing `ssh`. It is just an ssh terminal, **so anything typed in will be sent to the remote device as a terminal command,** like the command `whoami` will give you the username of the Raspberry Pi.
  - cmd:
    Obviously the command to access this is `cmd`. This is just a **regular local cmd terminal,** nothing special.

- ### Sending all files
  After making the connection, the `Create connection` button changes to `Connected features`. Pressing it will make a little menu appear on top. The button, called `Send files` **will send over all files and subdirectories in the `Folder Path` folder to the `Send Folder Path` folder on the remote device** (This is basically just a shortcut to writing `send_all` into the cc terminal).

- #### Backup files
  The third button, `Create backup` will first ask for a name then a description, **after which it will create a new folder in the `Backup Folder`** with the files in the `Folder Path`. There is also a `Choose backup button`, **however at this moment it does not do anything** except showing all the backups already made.

options
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

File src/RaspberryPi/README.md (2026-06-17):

# Raspberry Pi code
The main file is [full.py](/src/RaspberryPi/full.py). The Open Challenge code starts at line `846`, Obstacle Challenge at line `1613`.

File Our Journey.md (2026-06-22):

# Our journey

In this segment, we'll focus on our development process throughout the years. The challenges we faced, the engineering decisions we made, and how the final design of our robot came to be.

## Our history in WRO

Before we begin talking about anything technical we think it is important to mention the past, because it might make it more clear why we made some decisions previously, and where our engineering experience stems from. It might be a bit long, but its hard to summarize so many years in just a few sentences.
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

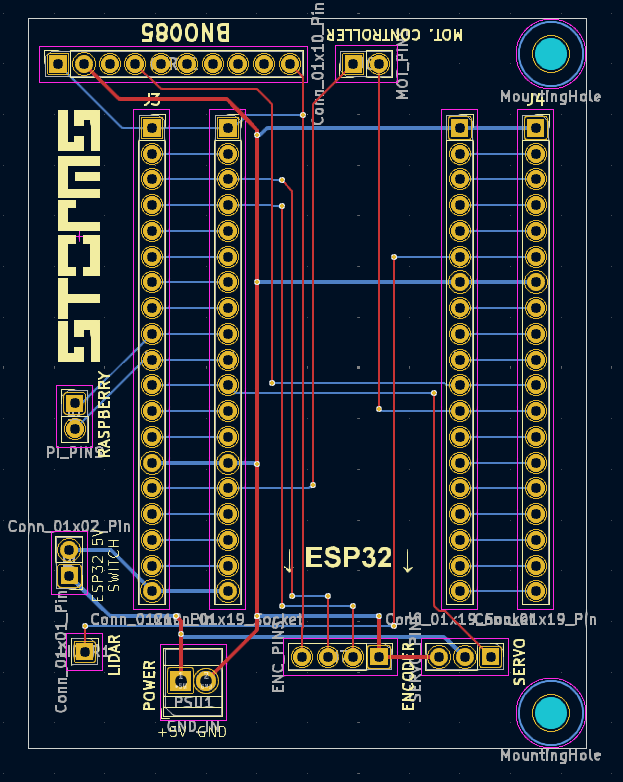
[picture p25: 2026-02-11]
schemes/PCB_design.png

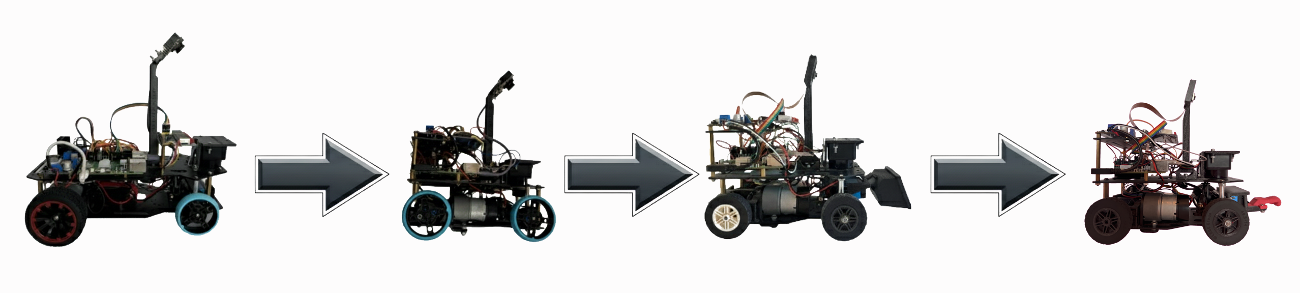
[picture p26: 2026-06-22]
evolution3.png

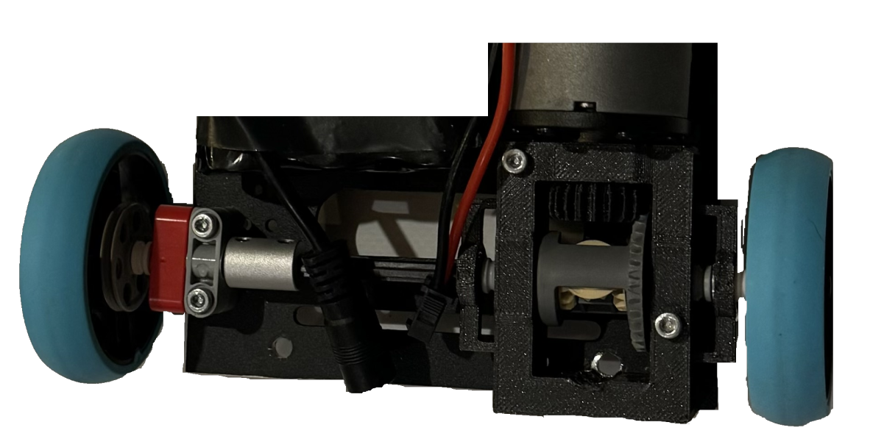
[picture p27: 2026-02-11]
diff.webp

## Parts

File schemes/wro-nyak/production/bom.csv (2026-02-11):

Designator | Footprint | Quantity | Value | LCSC Part #
GYRO1 | PinSocket_1x10_P2.54mm_Vertical | 1 | Conn_01x10_Pin | C57369
J1, J2 | PinSocket_1x19_P2.54mm_Vertical | 2 | Conn_01x19_Socket | C2897382
J3, J4 | PinSocket_1x19_P2.54mm_Vertical | 2 | Conn_01x19_Pin | C2897382
J5 | PinHeader_1x02_P2.54mm_Vertical | 1 | PI_PINS | C2905434
J6 | PinHeader_1x02_P2.54mm_Vertical | 1 | MOT_PINS | C2905434
J7 | PinHeader_1x04_P2.54mm_Vertical | 1 | ENC_PINS | C2905435
J8 | PinHeader_1x03_P2.54mm_Vertical | 1 | SERVO_PINS | C2932698
J9 | PinHeader_1x02_P2.54mm_Vertical | 1 | Conn_01x02_Pin | C2905434
LIDAR1 | PinHeader_1x01_P2.54mm_Vertical | 1 | Conn_01x01_Pin | C81276
PSU1 | TerminalBlock_Xinya_XY308-2.54-2P_1x02_P2.54mm_Horizontal | 1 | GND_IN | C5188442

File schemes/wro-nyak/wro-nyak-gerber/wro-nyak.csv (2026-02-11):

Id | Designator | Footprint | Quantity | Designation | Supplier and ref
1 | PSU1 | TerminalBlock_Phoenix_MPT-0,5-2-2.54_1x02_P2.54mm_Horizontal | 1 | GND_IN
2 | GYRO1 | PinSocket_1x10_P2.54mm_Vertical | 1 | Conn_01x10_Pin
3 | J8 | PinHeader_1x03_P2.54mm_Horizontal | 1 | SERVO_PINS
4 | J2,J1 | PinSocket_1x19_P2.54mm_Vertical | 2 | Conn_01x19_Socket
5 | J5 | PinHeader_1x02_P2.54mm_Vertical | 1 | PI_PINS
6 | J4,J3 | PinSocket_1x19_P2.54mm_Vertical | 2 | Conn_01x19_Pin
7 | J6 | PinHeader_1x02_P2.54mm_Vertical | 1 | MOT_PINS
8 | J7 | PinHeader_1x04_P2.54mm_Horizontal | 1 | ENC_PINS
9 | LIDAR1 | PinHeader_1x01_P2.54mm_Horizontal | 1 | Conn_01x01_Pin

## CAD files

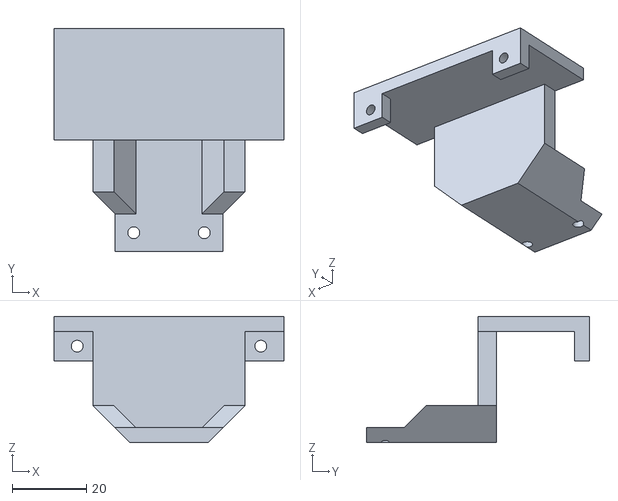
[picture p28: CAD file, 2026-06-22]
models/bumper_mount.stl
62.0 x 60.0 x 34.0

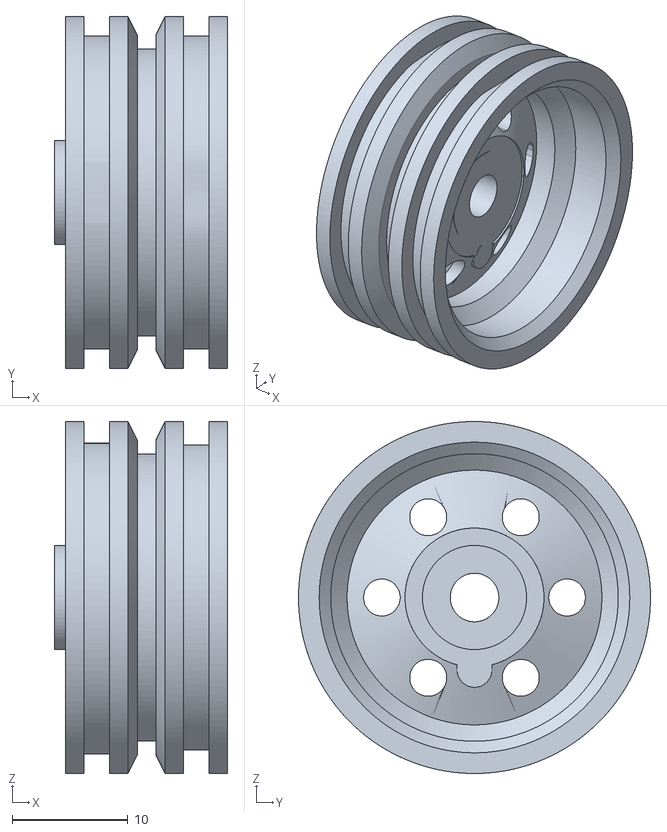
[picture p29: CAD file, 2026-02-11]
schemes/nutted wheel.stl
15.0 x 30.4 x 30.4

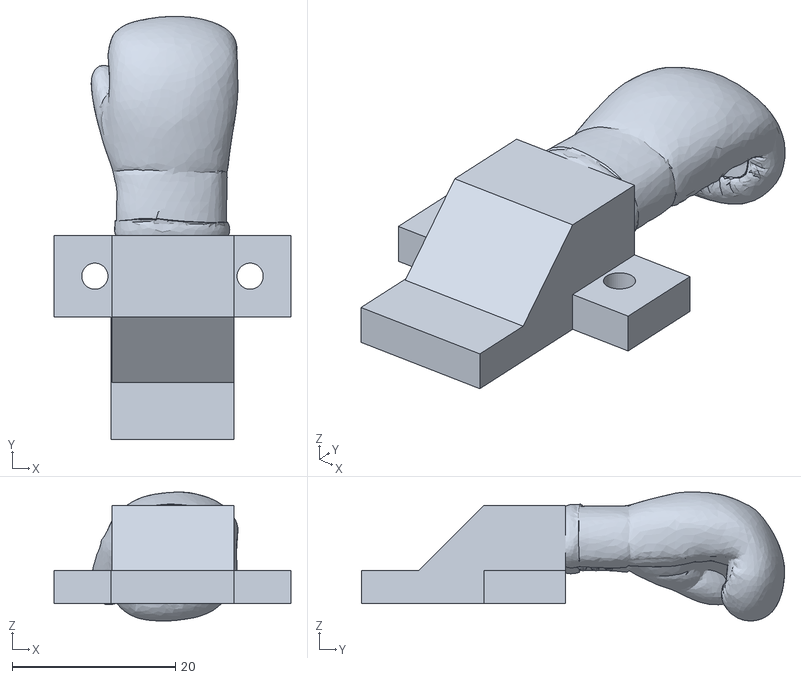
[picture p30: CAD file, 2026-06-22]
models/glove.stl
29.0 x 51.8 x 15.8

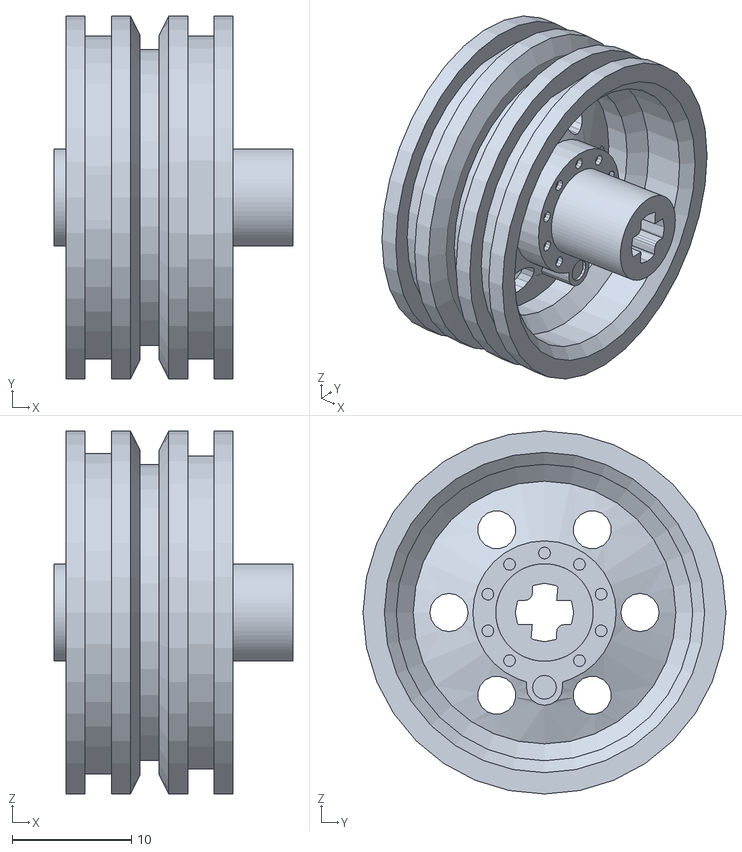
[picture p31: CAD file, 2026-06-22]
models/normal wheel.stl
20.0 x 30.4 x 30.4

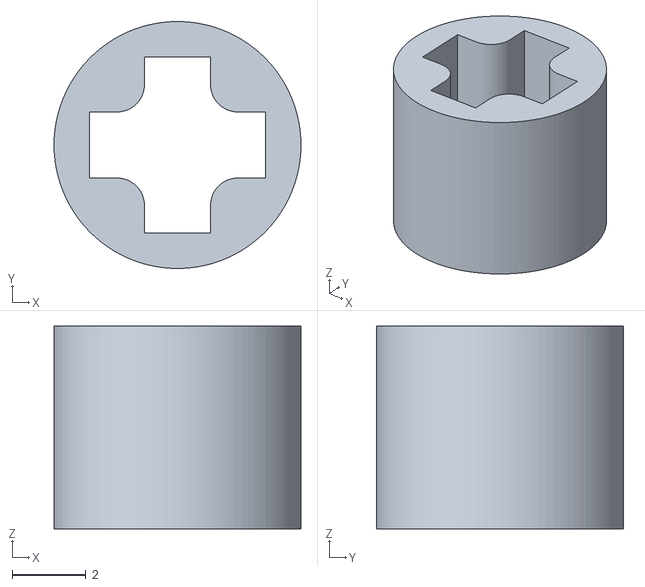
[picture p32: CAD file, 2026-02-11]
models/ring.stl
6.70 x 6.70 x 5.50

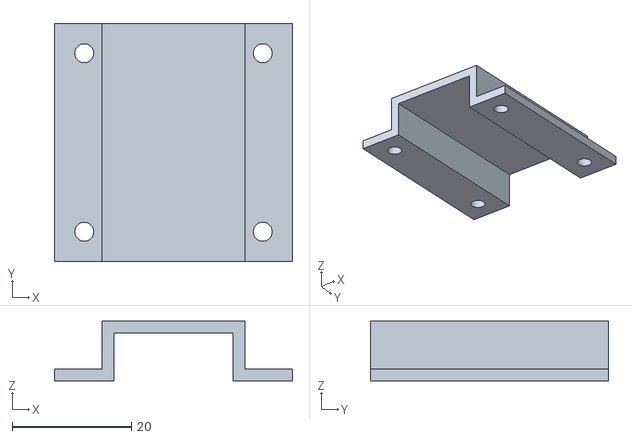
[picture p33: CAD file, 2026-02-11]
models/tunnel.stl
40.0 x 40.0 x 10.0

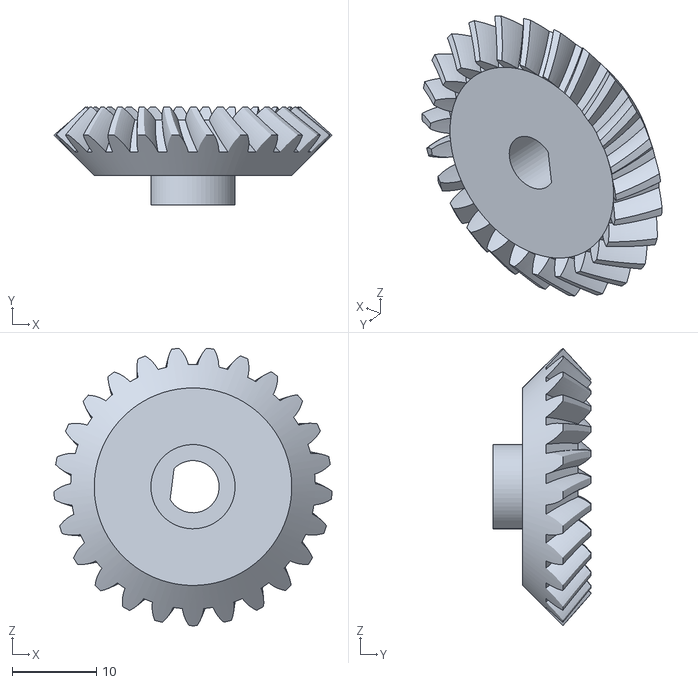
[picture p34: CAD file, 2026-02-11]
models/diff cog.stl
33.0 x 11.6 x 32.9

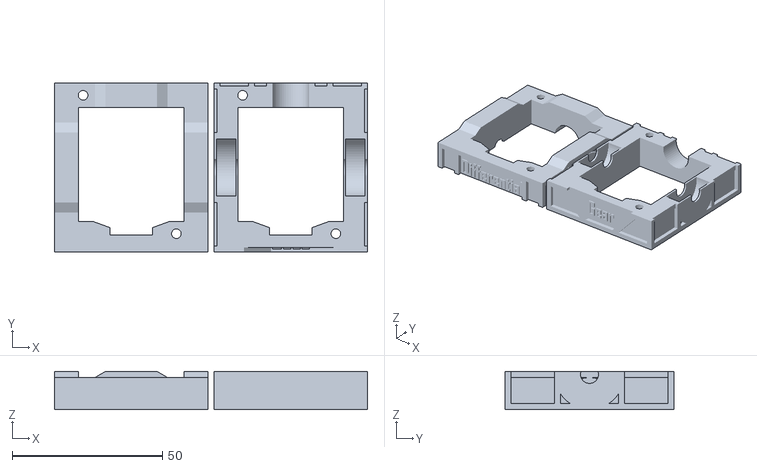
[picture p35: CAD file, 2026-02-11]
models/diff frame.stl
104.0 x 56.0 x 12.7

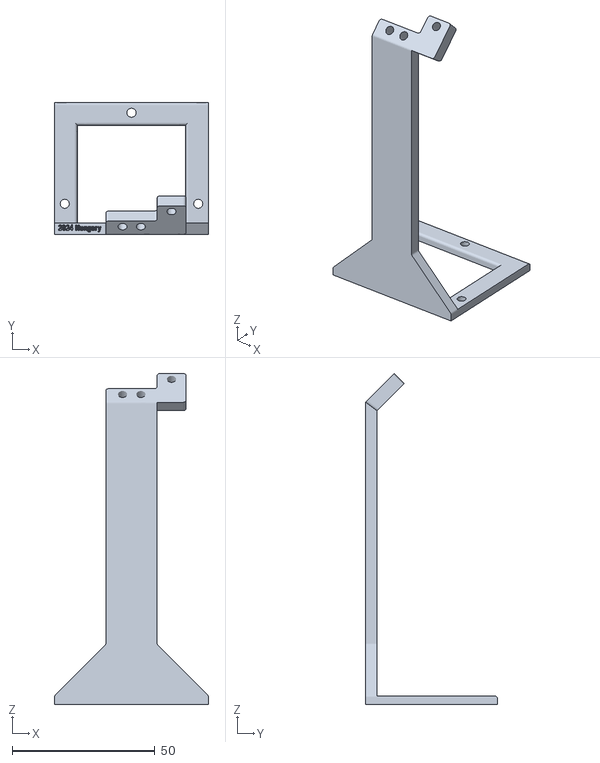
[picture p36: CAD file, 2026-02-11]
models/Camera stand.stl
54.0 x 46.3 x 116.0

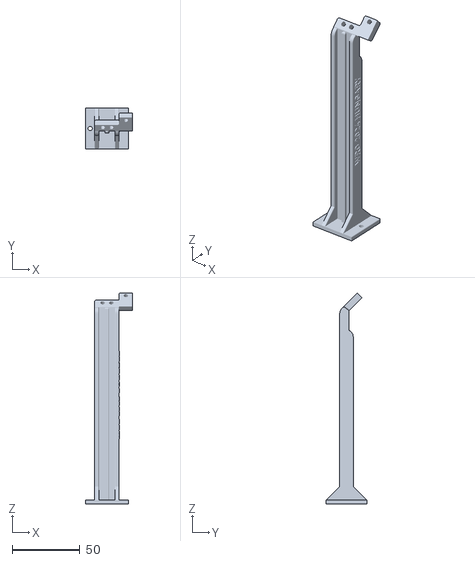
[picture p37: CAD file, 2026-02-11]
models/Camera stand 3 v2.stl
35.1 x 30.0 x 156.0

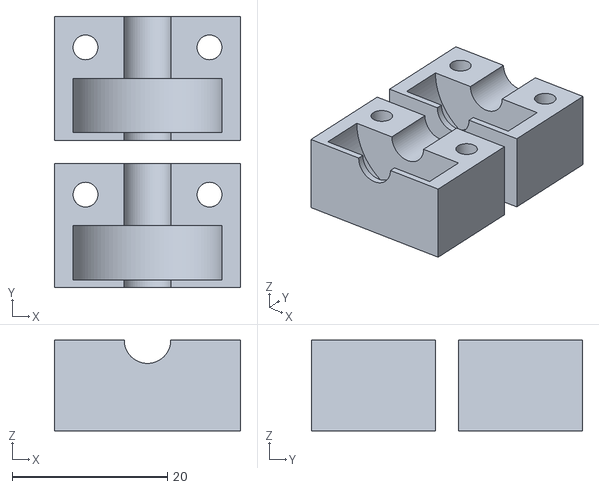
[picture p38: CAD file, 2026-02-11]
models/axle holder.stl
24.0 x 35.0 x 11.7

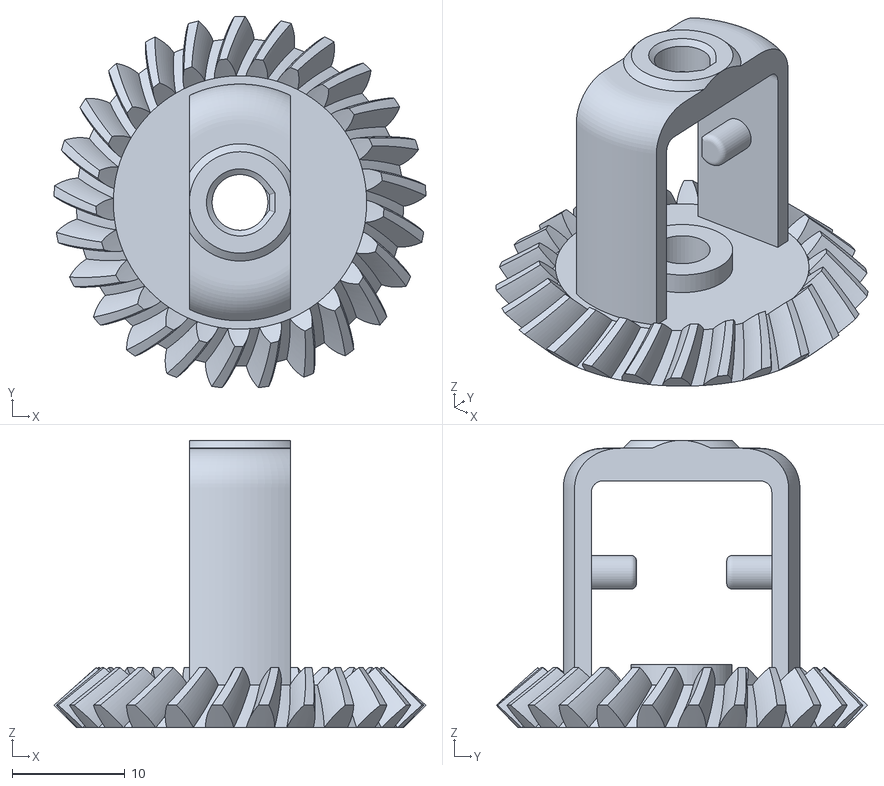
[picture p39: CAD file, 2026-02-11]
models/diff.stl
33.0 x 32.9 x 25.5

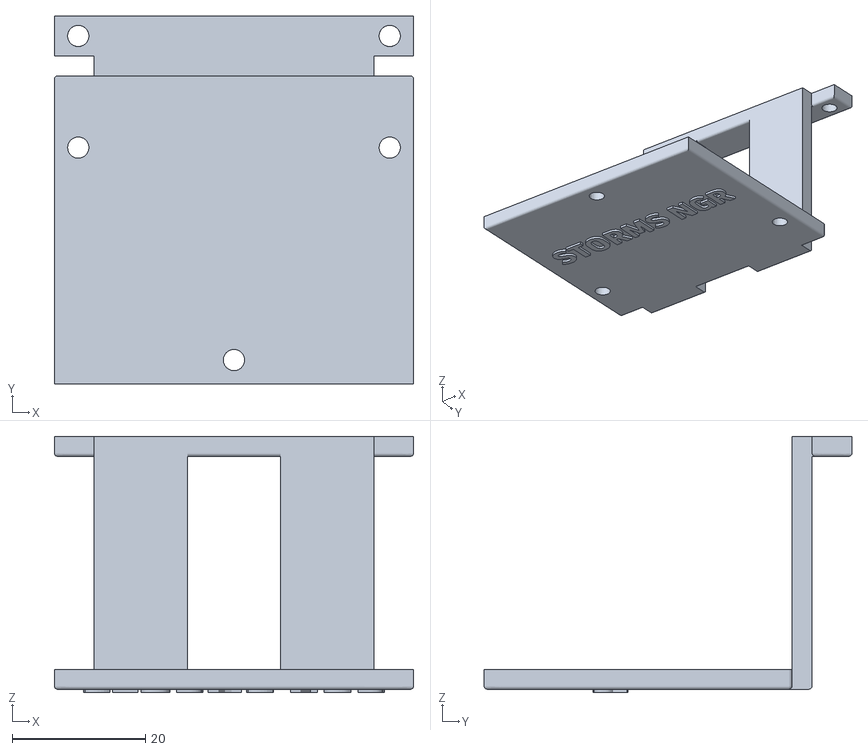
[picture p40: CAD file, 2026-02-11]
models/Lidar stand.stl
54.0 x 55.3 x 38.5

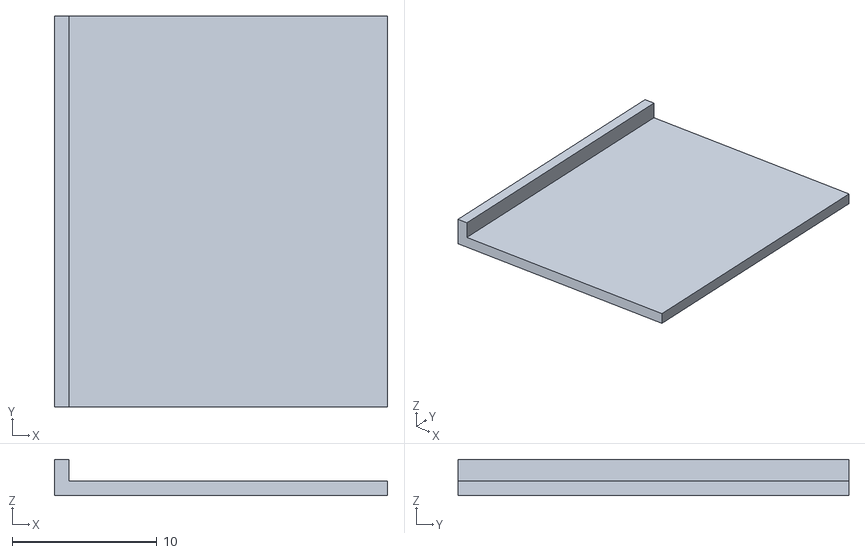
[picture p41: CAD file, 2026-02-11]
models/lid.stl
23.0 x 27.0 x 2.50

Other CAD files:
schemes/wheel original.stl
models/Camera final.stl
models/Camera stand 2 v1.stl
models/Lidar mount.stl
models/Camera final.f3d
models/Camera stand 2 v1.f3d
models/Camera stand 2 v2.f3d
models/Camera stand 2 v3.f3d
models/Camera stand 3 v1.stl
models/Camera stand.f3d
models/Lidar mount.f3d
models/Lidar_mount.f3d
models/axle holder.f3d
models/bumper_mount.f3d
models/diff cog.f3d
models/diff frame.f3d
models/diff.f3d
models/lid.f3d
models/normal wheel.f3d
models/ring.f3d
models/tunnel.f3d
schemes/nutted wheel.f3d

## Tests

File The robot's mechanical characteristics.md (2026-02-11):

# The robot's mechanical characteristics

In this section we will write about different kinds of tests we had our robot do in order to **gather data about its precision.** These data allowed us to draw conclusions that could help us calibrate our runs and **fix any instability issues that might occur.**

## Deviation from parallel at varying speeds

In this test we had our robot go in a parallel line and then measure how **much it deviated perpendicularly to the parallel.**
In each measurement we used a **different speed, but the same distance,** since the deviation is proportional to the distance when going straight in a smooth movement. At first glance the speeds we used seem random however this is due to the fact that **our robot measures velocity in internal encoder "tick"/second rather than meter/second,** so we had to convert it using the diameter of the wheels, the ratio of the motor and the differential gearbox, and the resolution of the encoder to finally get cm/s. (12.4 t/s = 1 cm/s)

| | v(cm/s) | x<sub>deviation </sub>(cm)|
| - | --- | --- |
| 1 | 9.682417  | 1.5 |
| 2 | 19.36483  | 1.5 |
| 3 | 29.04725  | 1.5 |
| 4 | 38.72967  | 1.6 |
| 5 | 48.41208  | 1.6 |
| 6 | 58.0945 | 1.6 |
| 7 | 67.77692  | 1.6 |

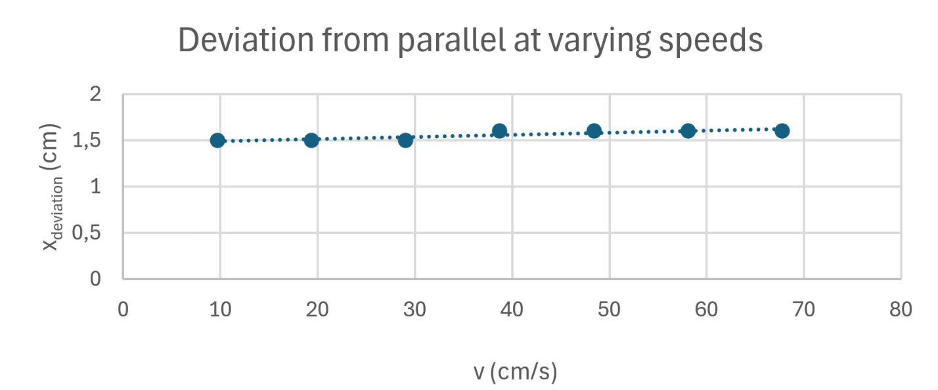
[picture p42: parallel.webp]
parallel


The conclusion we can draw from this is that the **change in deviation from the speed is negligible** enough, so that we can use any speed we desire, but there is still a constant amount of base deviation, that thankfully can be fixed by adding a **constant multiplier** in the code.

## Distance detection at varying speeds

For this test we had our robot go in a straight line until it got in a 50 cm distance of the object in front of it. The purpose of this test is to **measure the latency of our lidar sensor,** which can be concluded from the extra distance the robot goes before realizing it is in the 50 cm range.

| | v(cm/s) | x<sub>deviation </sub>(cm)|
| - | --- | --- |
| 1 | 9.682417  | 0.6 |
| 2 | 19.36483  | 0.5 |
| 3 | 29.04725  | 1.3 |
| 4 | 38.72967  | 1.2 |
| 5 | 48.41208  | 1.4 |
| 6 | 58.0945 | 3.4 |
| 7 | 67.77692  | 1.3 |

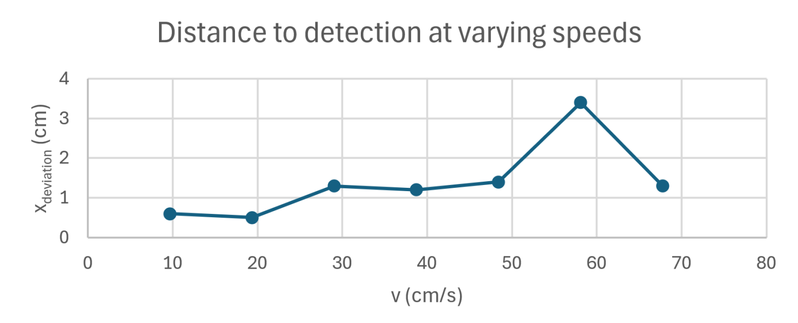
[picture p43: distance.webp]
distance


This data at first seems to be chaotic but after thinking about it there is a very reasonable explanation for this behavior. The lidar sensor spins around 10 times per second. This means that when the robot goes with, for example 48 cm/s, in one revolution or between two measurements, it could go 4.8 cms, **so it depends on both the speed and the lidar's current position.** Thankfully this deviation does not add up, because we are getting a new measurement at every turn. For the obstacle challenge we are going slowly most of the time **immensely reducing the maximum amount of deviation** we could get. We concluded that to speed up to open challange we will have to also speed up the LiDAR, which was possible, up to 15 times a second. This did present other challenges, which are detailed in the [software documentation](/src/README.md#sensors-and-motors).

## Brake distance at varying speeds

In the previous test after the robot sensed that it is in range it started breaking and each time **we measured the break distance.** Being able to calculate brake distances can be crucial if we want to make **precise movements.** 

| | v(cm/s) | x<sub>deviation </sub>(cm)|
| - | --- | --- |
| 1 | 9.682417  | 1.3 |
| 2 | 19.36483  | 2.6 |
| 3 | 29.04725  | 3.4 |
| 4 | 38.72967  | 5.3 |
| 5 | 48.41208  | 7.6 |
| 6 | 58.0945 | 9.5 |
| 7 | 67.77692  | 12.2 |

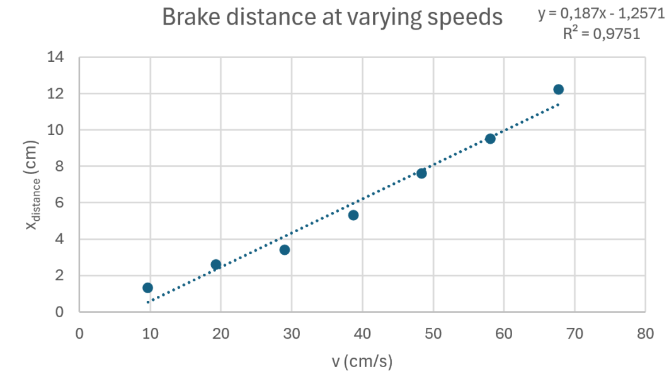
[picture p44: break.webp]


As we can see from the diagram **the correlation between the brake distance and velocity is basically linear,** which massively simplifies the process of calculating.

## Angle deviation at varying speeds

The last test we did was check much the robot would say it actually turned when we tell it to turn 90 degrees at different speeds. The amount we give it shouldn't really matter since we are not testing the gyro's accuracy, we are testing how well it can turn according to what the gyro tells it, so this is how well the **internal turning control** algorithm works, not how accurate the **gyro** is.

| | v(m/s) | φ(°) |
| - | --- | ---- |
| 1 | 9,682417 | 2,9  |
| 2 | 19,36483 | 2,8  |
| 3 | 29,04725 | 2,9  |
| 4 | 38,72967 | 2,8  |
| 5 | 48,41208 | 2,9  |
| 6 | 58,0945  | 2,7  |

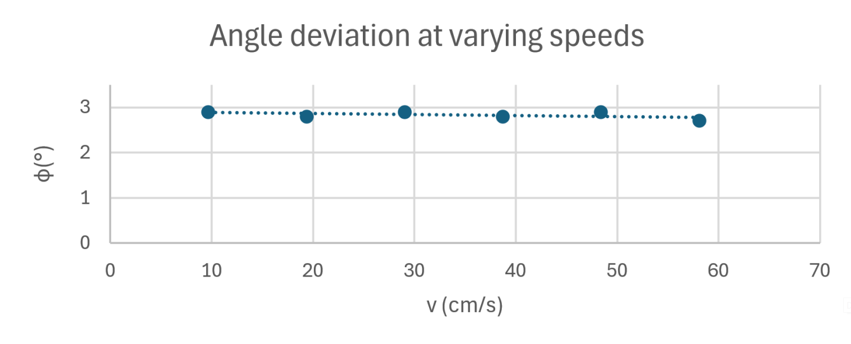
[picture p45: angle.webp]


Same as with the parallels, the speed of the robot does not seem to determine the deviation, since **it is practically a constant number,** making it something that can easily be **corrected by adding a constant** to the calculations in the code. We concluded that his constant is releated to the turning speed of the servo. Since the servo isn't instantenious, when we reach the target angle the robot will continue turning for a bit until the servo straightens. We combatted this the introduction of `predictedYaw` which calculates at what angle the robot will be in the future, exactly by how many seconds the servo takes to straighten, so the robot can stop turning then.

# Conclusion

In conclusion these measurements **massively helped us** when optimizing for the run, since it showed some critical inaccuracies, which if left unchecked **could have cause some serious problems** in our runs. It also helped us to understand our robot's capabilities and limits just a little better.

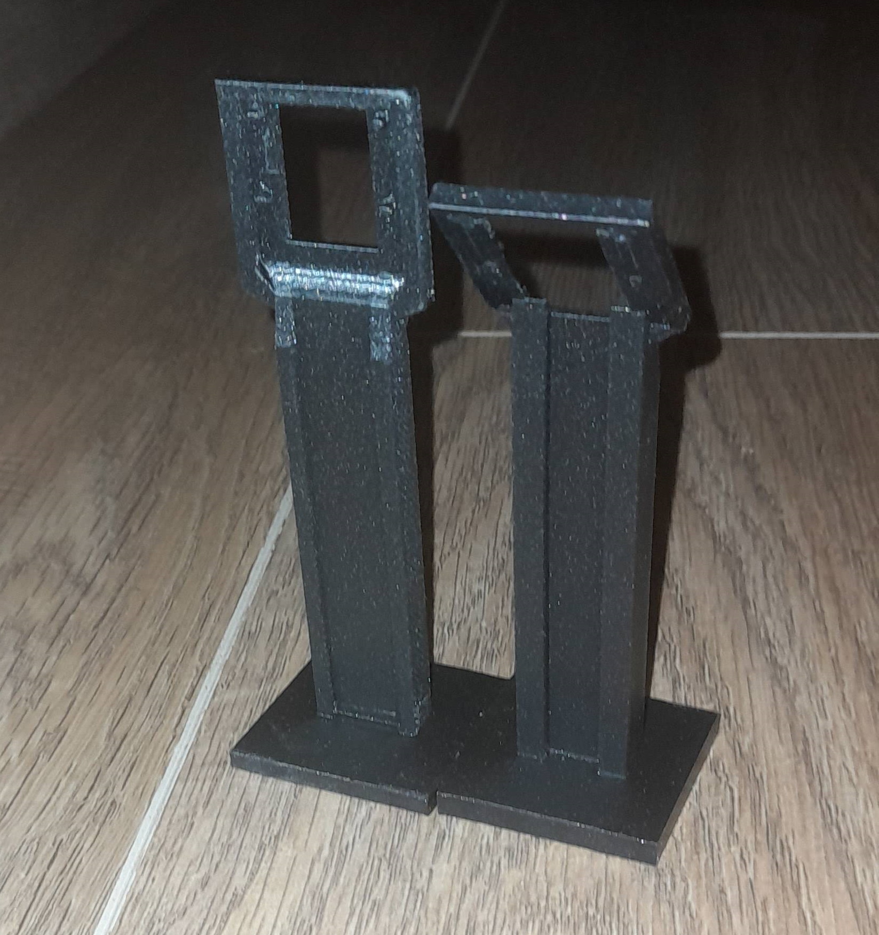
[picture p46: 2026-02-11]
test.jpg

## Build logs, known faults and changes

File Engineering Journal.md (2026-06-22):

# Engineering Journal
This document shows our progress in a monthly basis. It is updated live during our preparation, beginning from the start of the 2026 season of Future Engineers, 2026. january.

## January
We begun by reading and interpreting the rules. Since the main challenge didn't change it was clear most of our time would be spent improving the documentation, and preparing for possible surprise rules. To start we looked at the top teams' documentation, looking for things to learn/improve, especially in scoring areas they achieved exceptional results in. 

A list of the different teams' documentation we reviewed with a short note of our takeaway:
- Team Double-X: Their solution is vastly different from ours, but their use of flowcharts and GitHub issues seem like a good idea
- Team KMIDS GFM: Their solution is more similar to ours, though they do rely more heavily on the camera. Initially we avoided this, but it might be something we have to attempt this year
- Team FireOnAllCylinders: Their Learning Journey is in part the inpsiration for this document
- Team ANTİ: Their robot is vastly different from ours. It's speed and form factor is outsanding, but it's not something we would attempt

## February
This month was uneventful, mainly because the first few weeks of university took up most of our time.

## March
`03.13.:` We finally dusted off the robot for some  tests. It performed remarkably well out of the box, but of course we had to fine-tune some calibrations. During this fine-tuning however we  managed to short-circuit our ESP, completely frying it in the process. This was a valuable lesson as this isn't the first time we managed to kill an ESP, so we will make sure to bring backup ones to the competition. Luckily we managed to get it replaced pretty quickly.

`03.25.:` RoboTech Challenge Day<br>
We were invited to the National/Central European demo competition RoboTech, where among other categories they had a WRO Future Engineers competition. It was a great opportunity for us to practice on a foreign track in different conditions, and the robot did not dissappoint, managing to score full points after some calibrations.

## April
`04.17.:` We discussed possible improvements of the robot, such as the creation of a new PCB and it's new features. We also decided to implement a new obstacle challenge strategy to reduce our time by a significant amount.

`04.28.:` We started work on creating the improved strategy. It will make the run much more complicated than before, and since simplicity and straight-forwardness is very important to us we had to make sure it remained clear and understandable. We made a work-in-progress flowchart, and started implementing parts of it. Whether we finish it for the nationals or not is not certain.  
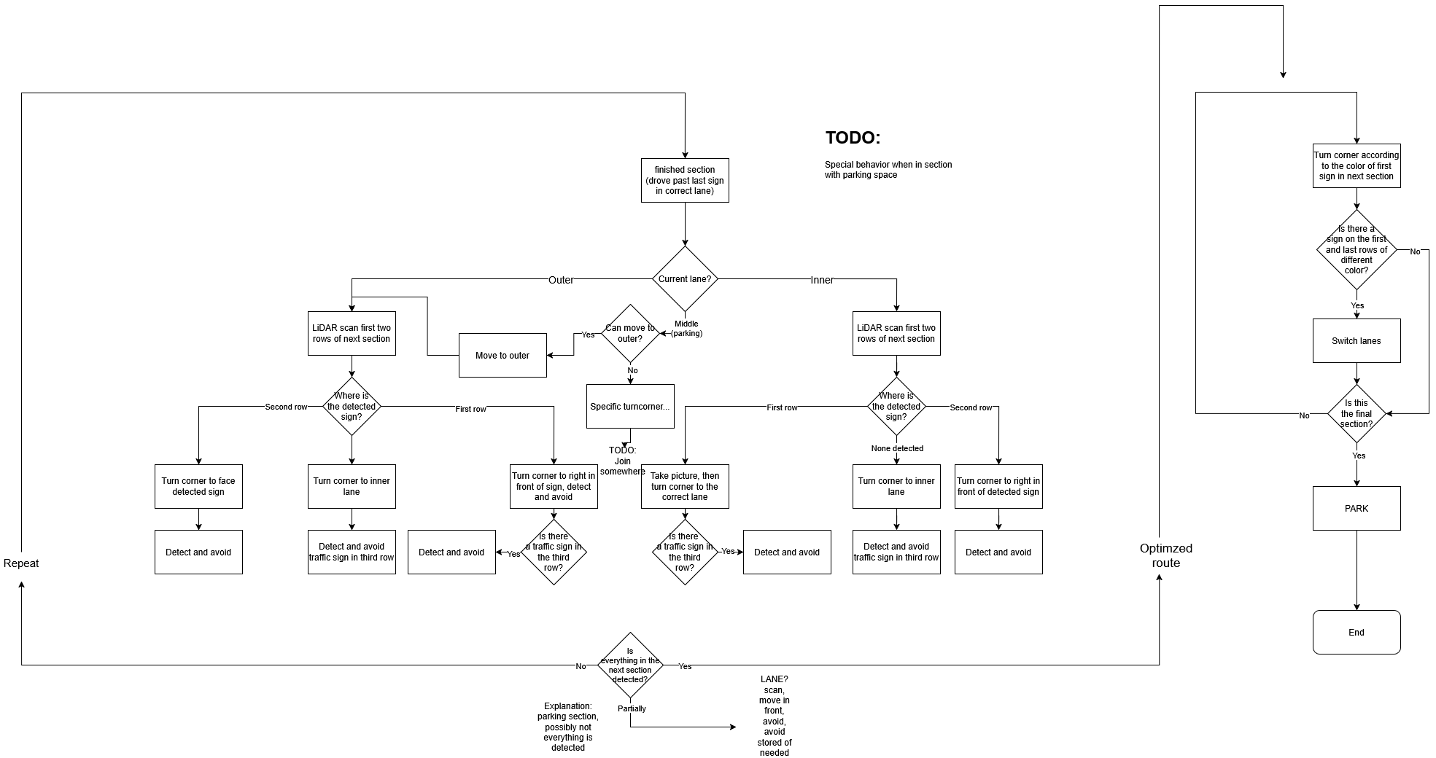
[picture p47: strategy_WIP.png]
WIP strategy


## May
We started implementing the new strategy in parts, and quickly realized this is not the way forward to the nationals. The number of cases grew exponentially and we didn't have enough time before the nationals to finish properly implementing it. We instead made a compromise between the new strategy and the old one that enables us to keep the simplicity of the old strategy with significant timesaves. After deciding on this strategy we quickly started implementing and testing it.

## June
`06.10.:` We finished implementing the strategy and tested it to our best ability. We are really happy with the results. We also had to start planning the documentation and preparing for the surprise rule.

`06.15.:` The surprise rule was announced. We prioritized solving it, pausing documentation work meanwhile. We managed to solve it fairly easily, but we also have to test the full run with the surprise rule thoroughly.

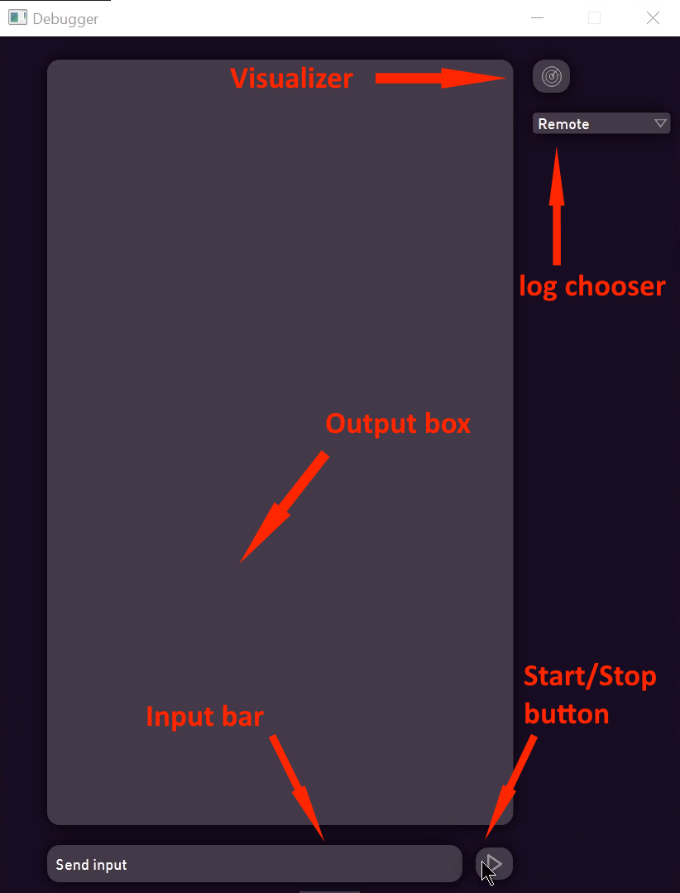
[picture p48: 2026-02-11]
other/Debugger.png

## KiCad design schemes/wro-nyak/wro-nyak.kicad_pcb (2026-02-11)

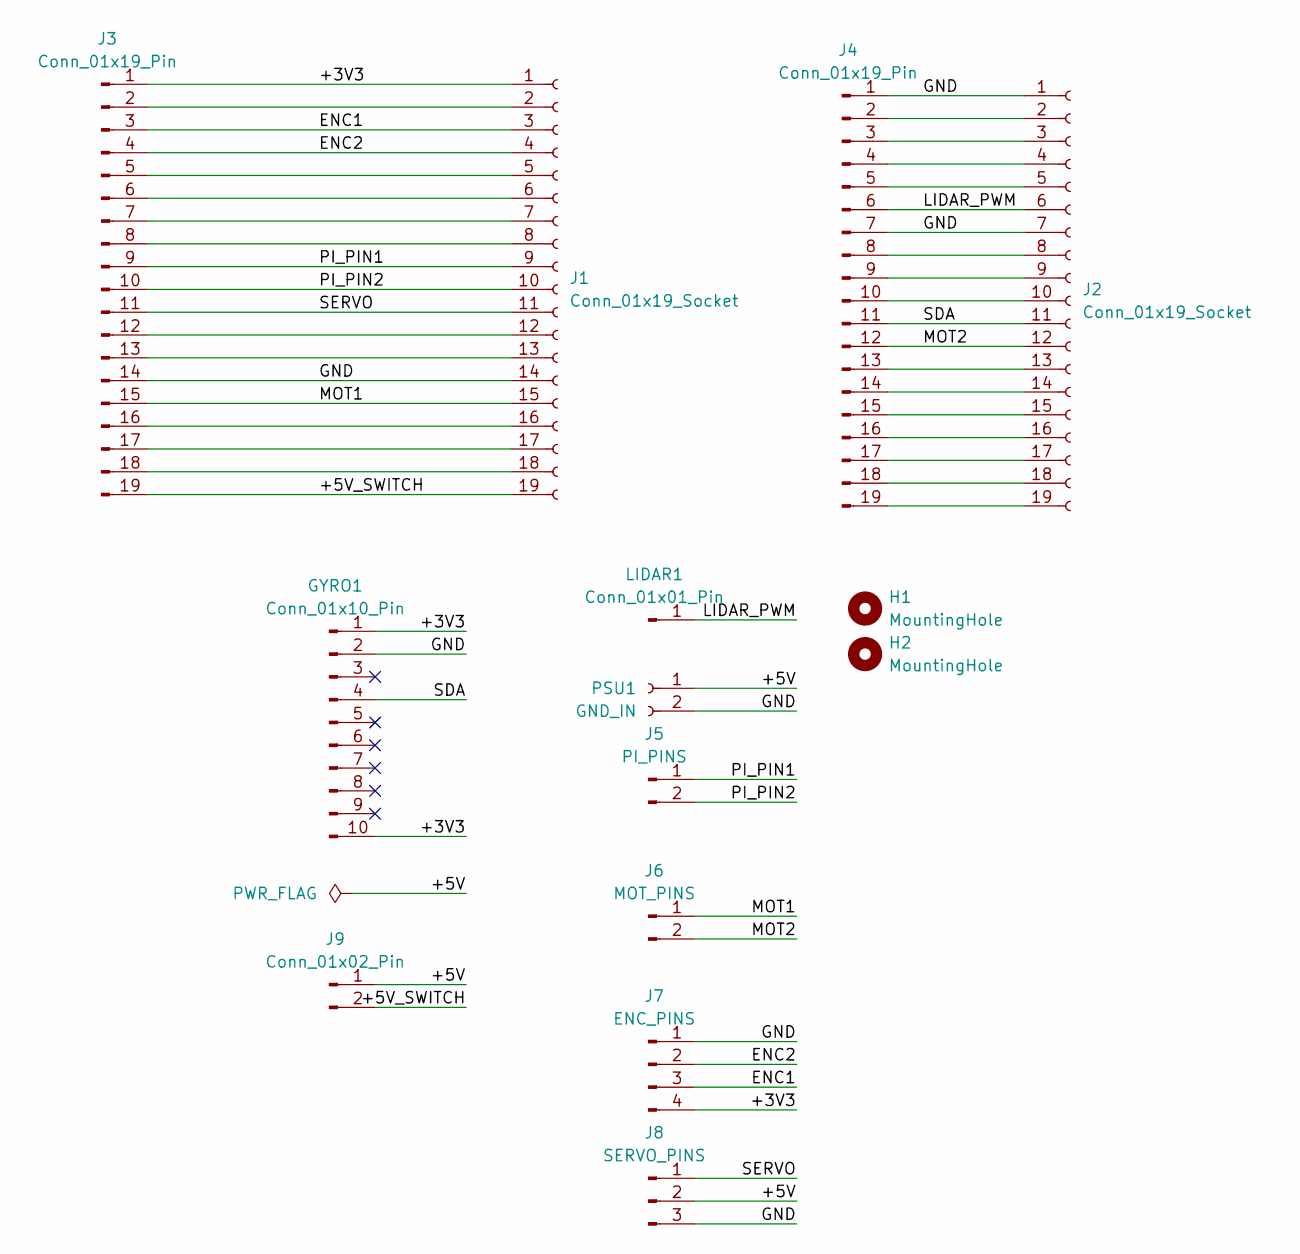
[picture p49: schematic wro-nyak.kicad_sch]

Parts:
GYRO1: Conn_01x10_Pin; PinSocket_1x10_P2.54mm_Vertical; LCSC C57369
H1, H2: MountingHole; MountingHole_3.2mm_M3
J1, J2: Conn_01x19_Socket; PinSocket_1x19_P2.54mm_Vertical; LCSC C2897382
J3, J4: Conn_01x19_Pin; PinSocket_1x19_P2.54mm_Vertical; LCSC C2897382
J5: PI_PINS; PinHeader_1x02_P2.54mm_Vertical; LCSC C2905434
J6: MOT_PINS; PinHeader_1x02_P2.54mm_Vertical; LCSC C2905434
J7: ENC_PINS; PinHeader_1x04_P2.54mm_Vertical; LCSC C2905435
J8: SERVO_PINS; PinHeader_1x03_P2.54mm_Vertical; LCSC C2932698
J9: Conn_01x02_Pin; PinHeader_1x02_P2.54mm_Vertical; LCSC C2905434
LIDAR1: Conn_01x01_Pin; PinHeader_1x01_P2.54mm_Vertical; LCSC C81276
PSU1: GND_IN; TerminalBlock_Xinya_XY308-2.54-2P_1x02_P2.54mm_Horizontal; LCSC C5188442

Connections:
/+3V3: GYRO1.1, GYRO1.10, J1.1, J3.1, J7.4
/+5V: J8.2, J9.1, PSU1.1
/+5V_SWITCH: J1.19, J3.19, J9.2
/ENC1: J1.3, J3.3, J7.3
/ENC2: J1.4, J3.4, J7.2
/GND: GYRO1.2, J1.14, J2.1, J2.7, J3.14, J4.1, J4.7, J7.1, J8.3, PSU1.2
/LIDAR_PWM: J2.6, J4.6, LIDAR1.1
/MOT1: J1.15, J3.15, J6.1
/MOT2: J2.12, J4.12, J6.2
/PI_PIN1: J1.9, J3.9, J5.1
/PI_PIN2: J1.10, J3.10, J5.2
/SDA: GYRO1.4, J2.11, J4.11
/SERVO: J1.11, J3.11, J8.1
unnamed: J1.2, J3.2
unnamed: J1.5, J3.5
unnamed: J1.6, J3.6
unnamed: J1.7, J3.7
unnamed: J1.8, J3.8
unnamed: J1.12, J3.12
unnamed: J1.13, J3.13
unnamed: J1.16, J3.16
unnamed: J1.17, J3.17
unnamed: J1.18, J3.18
unnamed: J2.2, J4.2
unnamed: J2.3, J4.3
unnamed: J2.4, J4.4
unnamed: J2.5, J4.5
unnamed: J2.8, J4.8
unnamed: J2.9, J4.9
unnamed: J2.10, J4.10
unnamed: J2.13, J4.13
unnamed: J2.14, J4.14
unnamed: J2.15, J4.15
unnamed: J2.16, J4.16
unnamed: J2.17, J4.17
unnamed: J2.18, J4.18
unnamed: J2.19, J4.19

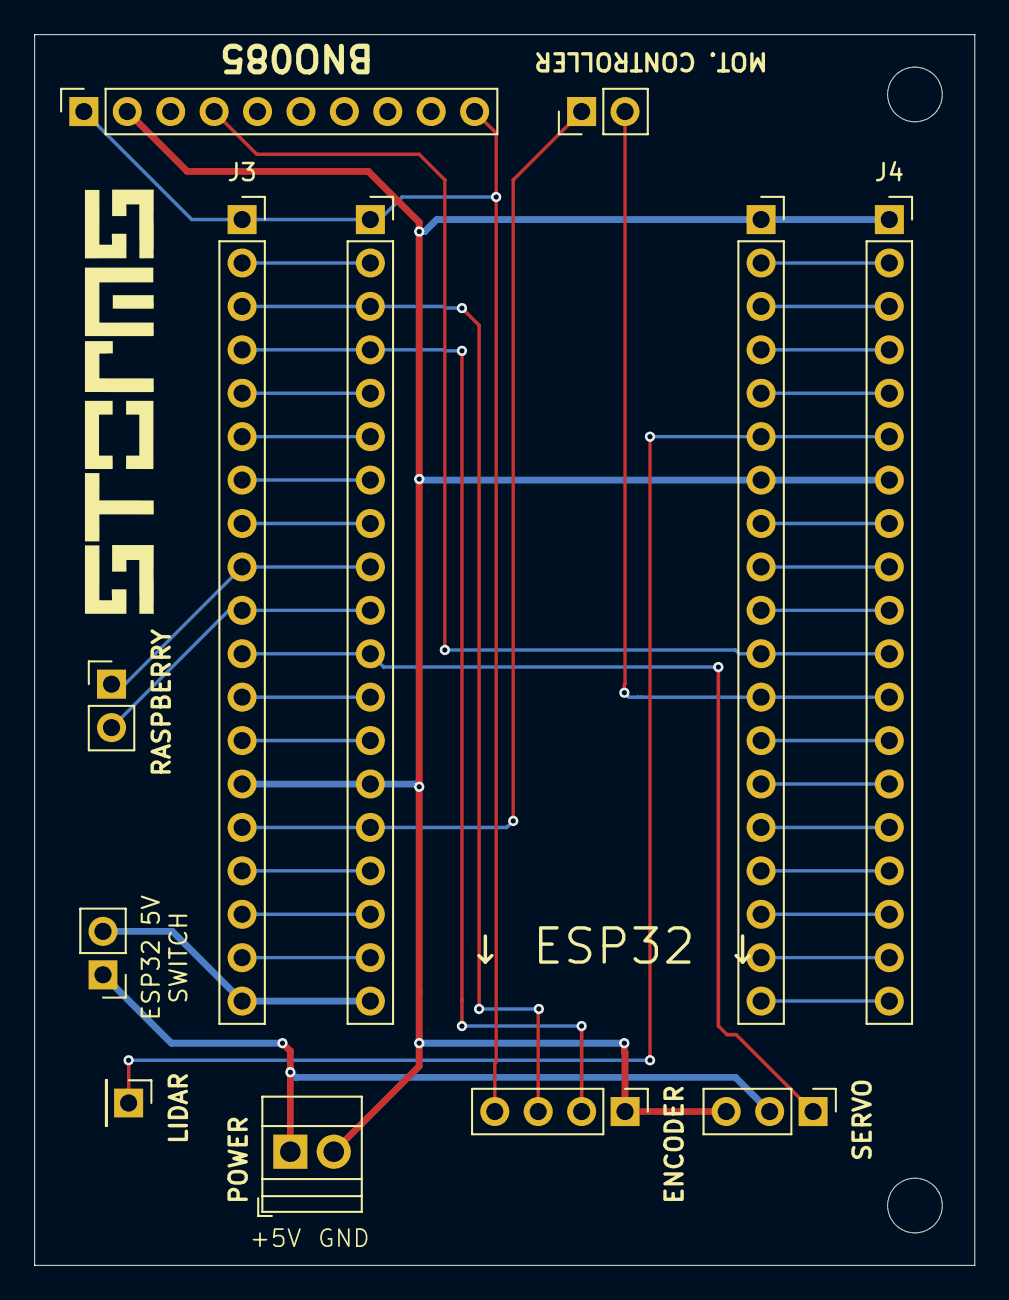
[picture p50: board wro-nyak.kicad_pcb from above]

Board: 2 copper layers, 55.0 x 72.0 mm, 14 parts (0 on the bottom side), 37 nets.

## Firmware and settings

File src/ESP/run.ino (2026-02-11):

#include <cmath>
#include <Wire.h> //I2C communication library
#include "Adafruit_BNO08x_RVC.h" //Gyroscope library

#define B_PIN_L 36 //Left motor encoder A pin
#define A_PIN_L 39 //Left motor encoder B pin
// #define PWM_PIN_L 21 //Left motor PWM pin (speed control)
#define PWM_BW_PIN 16 //Backward PWM pin
#define PWM_FW_PIN 13 //Forward PWM pin
#define A_PIN_R 35 //Right motor encoder A pin
#define B_PIN_R 34 //Right motor encoder B pin
// #define PWM_PIN_R 16 //Right motor PWM pin (speed control)
#define LED_PIN 2 //Built-in Led on the ESP
#define S_PWM_PIN 27 //Servo PWM pin (turning)
#define SRL_TX_PIN 25 //Serial communication TX pin (with raspberry)
#define SRL_RX_PIN 26 //Serial communication RX pin (with raspberry)
#define IMU_RX_PIN 17 //Serial communication receive pin (gyroscope)
#define IMU_TX_PIN 32 //Serial communication transmit pin (gyroscope)
#define US_TRIGGER_PIN -1 //Ultrasonic sensor trigger pin (send soundwave) (NOT CONNECTED)
#define US_ECHO_PIN -1 //Ultrasonic sensor echo pin (on measurement done) (NOT CONNECTED)
#define LIDAR_PWM_PIN 21 //LiDAR pwm speed control pin (18)


#define spwm_freq 50 //servo PWM frequency
#define spwm_res 12 //servo PWM resolution (2^12)
// #define spwm_channel 0 //servo PWM channel
#define motor_pwm_freq 19000 //motor PWM frequency

#define motor_pwm_res 12 //motor PWM resolution (2^12)

#define lidar_pwm_res 12 //lidar speed PWM resolution (2^10)
#define lidar_pwm_freq 1000 //lidar speed PWM frequency
#define LIDAR_PWM_SLOW 2211 //middle


#define I2C_ADDRESS 0x8 //I2C address of this ESP device

//Commands: These are used in the communication between the ESP and the raspberry
#define CMD_SYNC 17 //Synchronization command (raspberry)
#define CMD_STEER  6 //Steering command
#define CMD_HEARTBEAT 7 //Heartbeat command signal
#define CMD_LOG 8 //(retrieve)Log command
#define CMD_SET_VMODE 9 //set vmode (velocity mode) command
#define CMD_SET_TARGETSPEED 10 //set target speed command
#define CMD_SET_SMODE 18 //set smode (steer mode) command
#define CMD_SET_BREAKPERCENT 19 //set breaking percentage command
#define CMD_SET_TARGET_YAW 20 //set target yaw (heading) command
#define CMD_SET_SERVO_MAX 21 //set the maximum servo state
#define CMD_SET_SERVO_MIN 22 //set the minimum servo state
#define CMD_SET_SERVO_CENT 23 //set the central servo state
#define CMD_SET_UNREG 25 //set unregulated motor power
#define CMD_SET_GYRO_P 26 //set straightkeeping p parameter
#define CMD_SET_GYRO_D 27 //set straightkeeping d parameter
#define CMD_SET_SPCTRL_P 28 //set speed control p parameter
#define CMD_SET_SPCTRL_D 29 //set speed control d parameter
#define CMD_SET_HANDBRAKE_P 30 //handbrake vmode p parameter
#define CMD_SET_HANDBRAKE_I 31 //handbrake vmode i parameter
#define CMD_SET_ARCDIR 32 //send arc direction
#define CMD_SET_GYRO_L_MILLIS 33 //set arc prediction millis
#define CMD_SET_SGYRO_LIMITS 34 //set smode gyro limits
#define CMD_SET_SPCTRL_I 35 //set speedcontrol i parameter
#define CMD_SET_GYROERROR 36 //set gyro error compensation value
#define CMD_SET_ARCCANCEL 37 //force stop arc

#define CMD_DATA_POSL 11 //retrieve left motor position command
#define CMD_DATA_POSR 12 // retieve right motor position command
#define CMD_DATA_POSAVG 13 // retieve average motor position command
#define CMD_DATA_VMODE 14 // retrieve vmode command
#define CMD_DATA_SPEED 15 // retieve current speed command (real speed, not target)
#define CMD_DATA_ABS_GYRO 16 //retieve "absolute" gyro (does not loop back after 180 degrees to -180)
#define CMD_DATA_US 24 //retieve ultrasonic sensor measaured distance

#define US_DELAY 50 //Ultrasonic sensor delay (how much delay should be between sensor readings in milliseconds)

#define LED_C 15 //led PWM channel, not used

#define SYNC_CODE 18 //synchronization command response

#define STATUS_SYNCING 1 //ESP is trying to sync with raspberry pi
#define STATUS_CONNECTED 2 //ESP is successfully connected to raspberry pi

#define PiSerial Serial1

//VModes (velocity modes)
#define V_FORWARD 1 //robot is moving forward
#define V_BACKWARD -1 //robot is moving backward
#define V_STOP 0 //robot is stationary
#define V_BRAKE -2 //robot is braking (counter drive)
#define V_UNREGULATED 2 //the motors are powered with a constatnt force without speed control
#define V_HANDBRAKE -3

//SModes (steer modes)
#define S_NONE 0 //no steering
#define S_GYRO 1 //gyro controlled steering (keeping the robot straight)
#define S_ARC 2 //turn until target angle has been reached

//PID constants for dribing the motors
int kP=2; //UP
int kI=0;
int kD=0;

//PID constants for steering
int kPY=5;
int kIY=0;
int kDY=0;

int SERVO_MIN=219; //maximum safe left state servo PWM
int SERVO_MAX=417; //maximum safe right state servo PWM
int SERVO_CENT=291; //calibrated central state servo PWM

int conn_state=STATUS_SYNCING;
int heartBeatT0=0; //last heartbeat time

int posL=0;
int posR=0;
// int posAvg=0;
int lastTicks=0;
int speed=0;
int targetSpeed=0;
int brakePowerPercent=10;
int unregPower=0;

volatile int distance, duration, usStart, lastUSread; //ultrasonic sensor variables
volatile bool usSent=false; //is expecting an ultrasonic echo

//driving PID variables
int integral=0;
int lastError=0;

int vMode=V_STOP;
int sMode=S_NONE;

volatile int sGyroLimits=100;

//arc variables
volatile int isArcing=false;
volatile int arcT0=-1;
volatile int arcSpeed=-1;
volatile int gyroLatencyMillis=7;
volatile bool arcCancel=false;

//steering PID variables
volatile int integralY=0;
volatile int lastYError=0;

//handbrake values
volatile int handbrakePos0=-1;
volatile int handbrakeP=200;
volatile int handbrakeI=0;
volatile int handbrakeIntegral=0;

//gyro variables
int lastYaw=0;
int yawOffset=0;
int newYaw=0;
int lastAbsYaw=0;
//Error /360°
int gyroError=14;
volatile int absYaw=0;
volatile int targetYaw=0;

volatile int arcDirection=-1; //-1:left, 1:right
#define ARC_RIGHT 1
#define ARC_LEFT -1
//retievable log variable
int log_var=0;
//stored response to i2c command
int i2cResponse=-1;

volatile int turnRatioL=1000;
volatile int turnRatioR=1000;

int steerPercentage=0;

Adafruit_BNO08x_RVC rvc = Adafruit_BNO08x_RVC(); //gyro communication class in RVC mode
// void setDrivingDirection(int dir){
//   if(dir==1){
//     digitalWrite(PWM_BW_PIN, LOW);
//     digitalWrite(PWM_FW_PIN, HIGH);
//   } else{
//     digitalWrite(PWM_BW_PIN, HIGH);
//     digitalWrite(PWM_FW_PIN, LOW);
//   }
  
// }
//Ultrasonic sensor distance calculating (on echo interrupt)
void echo(){
  if(usSent){
    duration = micros()-usStart;
    int newDistance = (duration*172);
    distance=(distance*8+newDistance*2)/10;
    usSent=false;
  }
}
//Ultrasonic sensor start measure
void sendUSPulse(){
	digitalWrite(US_TRIGGER_PIN, LOW);
  delayMicroseconds(2);
  digitalWrite(US_TRIGGER_PIN, HIGH);
	delayMicroseconds(10);
	digitalWrite(US_TRIGGER_PIN, LOW);
  usStart=micros();
  usSent=true;
}

//timer interrupt, run exactly 100 times a second, handles real speed calulation, PID driving motor control and PID steering control
void IRAM_ATTR onTick(){
  // posAvg=(posL+posR)/2;
  speed=(speed*80+(((posR-lastTicks) * 100)*20))/100;
  lastTicks=posR;
  
  switch(sMode){
    case S_NONE:
    {
      int duty=-1;
      if(steerPercentage>0){
        duty=(SERVO_MAX-SERVO_CENT)*abs(steerPercentage)/100+SERVO_CENT;
      } else {
        duty=SERVO_CENT-(SERVO_CENT-SERVO_MIN)*abs(steerPercentage)/100;
      }
      if(duty>SERVO_MAX) {duty=SERVO_MAX;}
      if(duty<SERVO_MIN) {duty=SERVO_MIN;}
      ledcWrite(S_PWM_PIN,duty);
      break;
    }
    case S_GYRO:
    {
      int yError=absYaw-targetYaw;
      integralY+=yError;
      volatile int percent=(kPY*yError+integralY*kIY+(yError-lastYError)*kDY)/10*-1;
      percent=max(-sGyroLimits,int(min(percent,sGyroLimits)));
      percent*=(vMode==V_BACKWARD)?-1:1;
      int duty=SERVO_CENT;
      if(percent>0){
        duty=(SERVO_MAX-SERVO_CENT)*abs(percent)/100+SERVO_CENT;
      } else {
        duty=SERVO_CENT-(SERVO_CENT-SERVO_MIN)*abs(percent)/100;
      }

      lastYError=yError;
      if(duty>SERVO_MAX) {duty=SERVO_MAX;}
      if(duty<SERVO_MIN) {duty=SERVO_MIN;}
      ledcWrite(S_PWM_PIN,duty);
      break;
    }
    case S_ARC:
    {
      if(true){
        int duty=-1;
        if(steerPercentage>0){
          duty=(SERVO_MAX-SERVO_CENT)*abs(steerPercentage)/100+SERVO_CENT;
        } else {
          duty=SERVO_CENT-(SERVO_CENT-SERVO_MIN)*abs(steerPercentage)/100;
        }
        if(duty>SERVO_MAX) {duty=SERVO_MAX;}
        if(duty<SERVO_MIN) {duty=SERVO_MIN;}
        ledcWrite(S_PWM_PIN,duty);
      }


      int predictedYaw=absYaw+arcSpeed*(gyroLatencyMillis/10);
      // int predictedYaw=absYaw;
      // Serial.println("pyawe:");
      // Serial.println(predictedYaw);
      // Serial.println("smode "+sMode+" targetyaw "+targetYaw+" arcdir "+arcDirection+" predictedyaw "+predictedYaw);
      if((((arcDirection==ARC_RIGHT && predictedYaw>=targetYaw) || (arcDirection==ARC_LEFT && predictedYaw<=targetYaw)) && isArcing)){
        isArcing=false;
        steer(0);
        arcT0=millis();
        // setLedStatus(STATUS_CONNECTED);
      }

      if(millis()>=arcT0+gyroLatencyMillis && !isArcing) {
        sMode=S_GYRO;
      }
      if(arcCancel) {
        arcCancel=false;
        isArcing=false;
        sMode=S_GYRO;
      }
      break;
    }
  }
  switch(vMode){
    case V_UNREGULATED:
    {
      if(unregPower>0){
        ledcWrite(PWM_BW_PIN, 0);
        ledcWrite(PWM_FW_PIN, int(4095/100*abs(unregPower)));
      } else{
        ledcWrite(PWM_FW_PIN, 0);
        ledcWrite(PWM_BW_PIN, int(4095/100*abs(unregPower)));
      }
      // ledcWrite(PWM_PIN_R, 1000);
      // ledcWrite(PWM_PIN_L, 1000);
      // ledcWrite(PWM_PIN_R, int(4095/100*abs(unregPower)));
      break;
    }
    case V_STOP:
    {
      // ledcWrite(PWM_PIN_L, 0);
      ledcWrite(PWM_BW_PIN, 0);
      ledcWrite(PWM_BW_PIN, 0);
      break;
    }
    case V_FORWARD:
    {
      // Serial.println("s, l ,r");
      // Serial.println(speed);
      // Serial.println(posL);
      // Serial.println(posR);
      int error=targetSpeed-speed;
      integral+=error;
      int PWM=kP*error+integral*kI+(error-lastError)*kD;
      lastError=error;
      PWM=std::max(-4095/10,PWM);
      PWM=std::min(4095,PWM);
      
      if(PWM<0){
        ledcWrite(PWM_FW_PIN, 0);
        ledcWrite(PWM_BW_PIN, abs(PWM));
      } else{
        ledcWrite(PWM_BW_PIN, 0);
        ledcWrite(PWM_FW_PIN, abs(PWM));
      }
      // ledcWrite(PWM_PIN_L, abs(PWM));
      // ledcWrite(PWM_PIN_R, abs(PWM));
      // ledcWrite(PWM_PIN_L, 1000);
      // ledcWrite(PWM_PIN_R, 1000);
      break;
    }
    case V_BACKWARD:
    {
      int error=targetSpeed-speed;
      integral+=error;
      int PWM=(kP*error+integral*kI+(error-lastError)*kD);
      PWM*=-1;

      lastError=error;
      PWM=std::max(-4095/10,PWM);
      PWM=std::min(4095,PWM);
      if(PWM<0){
        ledcWrite(PWM_BW_PIN, 0);
        ledcWrite(PWM_FW_PIN, abs(PWM));
      } else{
        ledcWrite(PWM_FW_PIN, 0);
        ledcWrite(PWM_BW_PIN, abs(PWM));
      }
      // ledcWrite(PWM_PIN_L, abs(PWM));
      // ledcWrite(PWM_PIN_R, abs(PWM));
      break;
    }
    case V_BRAKE:
    {
      if(abs(speed)<100){
        handbrakePos0=posR;
        handbrakeI=0;
        vMode=V_STOP;
        break;
      }
      int brake=brakePowerPercent*pow(2,motor_pwm_res)/100;
      if(speed<0){
        ledcWrite(PWM_BW_PIN, 0);
        ledcWrite(PWM_FW_PIN, std::min(brake,4095));
      } else {
        ledcWrite(PWM_BW_PIN, std::min(brake,4095));
        ledcWrite(PWM_FW_PIN, 0);

      }
      
      // ledcWrite(PWM_PIN_R, brake);
      break;
    }
    case V_HANDBRAKE:
    {
      ledcWrite(PWM_BW_PIN, 4095);
      ledcWrite(PWM_FW_PIN, 4095);
      // int PWM=0;
      // int error=posR-handbrakePos0;
      // handbrakeIntegral+=error;
      // if(abs(error)>10){
      //   PWM=error*handbrakeP+handbrakeIntegral*handbrakeI;
      //   if(PWM<0){
      //     ledcWrite(PWM_BW_PIN, 0);
      //     ledcWrite(PWM_FW_PIN, std::min(4095,abs(PWM)));
      //   } else {
      //     ledcWrite(PWM_FW_PIN, 0);
      //     ledcWrite(PWM_BW_PIN, std::min(4095,abs(PWM)));
      //   } 
      // } else{
      //   ledcWrite(PWM_BW_PIN, 0);
      //   ledcWrite(PWM_FW_PIN, 0);
      //   PWM=0;
      // }
      // ledcWrite(PWM_PIN_L, std::min(4095,abs(PWM)));
      // ledcWrite(PWM_PIN_R, std::min(4095,abs(PWM)));

      break;
    }
  }
}

void setup() {
  // begin
  Serial.begin(115200);
  Serial.println("START");
  //driving PWM setup
  // ledcAttach(PWM_PIN_L, motor_pwm_freq, motor_pwm_res);
  ledcAttachChannel(PWM_BW_PIN, motor_pwm_freq, motor_pwm_res, 0);
  ledcAttachChannel(PWM_FW_PIN, motor_pwm_freq, motor_pwm_res, 2);
  // ledcAttach(PWM_PIN_R, motor_pwm_freq, motor_pwm_res);

  //lidar PWM speed control setup
  // pinMode(LIDAR_PWM_PIN, OUTPUT);
  // digitalWrite(LIDAR_PWM_PIN, LOW);
  ledcAttachChannel(LIDAR_PWM_PIN, lidar_pwm_freq, lidar_pwm_res, 4);
  // ledcAttach(LIDAR_PWM_PIN, lidar_pwm_freq, lidar_pwm_res);
  Serial.println("succesfull?");
  Serial.println(ledcWrite(LIDAR_PWM_PIN, 2048)); //enable PWM control
  delay(1000);
  ledcWrite(LIDAR_PWM_PIN,3440);
  delay(1000);
  ledcWrite(LIDAR_PWM_PIN, 0);

  // ledcDetach(LIDAR_PWM_PIN);
  // delay(3000);
  // ledcChangeFrequency(LIDAR_PWM_PIN, 30, lidar_pwm_res);
  // ledcWrite(LIDAR_PWM_PIN, 700);
  // pinMode(LIDAR_PWM_PIN, OUTPUT);
  // digitalWrite(LIDAR_PWM_PIN, LOW);
  // ledcWrite(LIDAR_PWM_PIN, 2048);

  //timer interrupts
  hw_timer_t *timer=NULL;
  timer=timerBegin(10000);
  timerAttachInterrupt(timer, &onTick);
  timerAlarm(timer,100,true,0);

  //servo pwm
  ledcAttachChannel(S_PWM_PIN, spwm_freq, spwm_res,6);
  ledcWrite(S_PWM_PIN, SERVO_CENT);

  //encoder
  pinMode(A_PIN_L, INPUT);
  pinMode(B_PIN_L, INPUT);
  pinMode(A_PIN_R, INPUT);
  pinMode(B_PIN_R, INPUT);
  attachInterrupt(digitalPinToInterrupt(A_PIN_L), readEncoder<'B','L'>, RISING);
  attachInterrupt(digitalPinToInterrupt(B_PIN_L), readEncoder<'A','L'>, RISING);
  attachInterrupt(digitalPinToInterrupt(A_PIN_R), readEncoder<'B','R'>, RISING);
  attachInterrupt(digitalPinToInterrupt(B_PIN_R), readEncoder<'A','R'>, RISING);
  //Ultrasonic sensor pins setup
  // pinMode(US_TRIGGER_PIN, OUTPUT);
  // pinMode(US_ECHO_PIN, INPUT);
  // attachInterrupt(digitalPinToInterrupt(US_ECHO_PIN), echo, FALLING); //function 'echo' gets called when measurement is done
  
  //led
  pinMode(LED_PIN,OUTPUT);
  // ledcAttachPin(LED_PIN, LED_C);
  // ledcSetup(LED_C, 4, 8);
  setLedStatus(STATUS_SYNCING);
  
  //Serial communication (raspberry)
  PiSerial.setPins(SRL_RX_PIN,SRL_TX_PIN);
  PiSerial.begin(115200);

  //IMU (gyro)
  Serial2.setPins(IMU_RX_PIN, IMU_TX_PIN);  
  Serial2.begin(115200);
  rvc.begin(&Serial2);

  //I2C COMM (raspberry)
  // Wire.setPins(I2C_SDA_PIN,I2C_SCL_PIN);
  // Wire.begin(I2C_ADDRESS);
  // Wire.onReceive(onI2CReceive);
  // Wire.onRequest(onI2CRequest);
  
}
//C++ template in order to avoid having to write 4 slightly different encoder pin detector methods. Keeps track of motors position.
template<char AorBToCheck,char side>
void readEncoder(){
  int pinToCheck=(AorBToCheck=='A' ? side=='L'? A_PIN_L : A_PIN_R  : side=='L' ? B_PIN_L : B_PIN_R);
  if(digitalRead(pinToCheck)==(AorBToCheck=='B')){
    side=='L' ? posL++ : posR--;
    
  } else {
    side=='L' ? posL-- : posR++;
    
  }
}
void setLedStatus(int status){
  switch(status){
    case STATUS_SYNCING:
      digitalWrite(LED_PIN,LOW);
      break;
    case STATUS_CONNECTED:
      digitalWrite(LED_PIN,HIGH);
      break;
  }
}
//called if sync between ESP and raspberry is broken, immediately stops all motors and resets the servo
void disconnect(){
  Serial.println("in disconnect");
  vMode=V_HANDBRAKE;
  steerPercentage=0;
  sMode=S_NONE;
  conn_state=STATUS_SYNCING;
  // ledcWrite(PWM_PIN_L,0);
  // ledcWrite(PWM_PIN_R,0);
  ledcWrite(PWM_BW_PIN, 0);
  ledcWrite(PWM_FW_PIN, 0);
  setLedStatus(STATUS_SYNCING);
}
//sends an int to the raspberry pi via serial
void sendInt(int data){
  for(int i=0;i<4;i++){
    PiSerial.write((data>>(8*i)) & 255);
  }
}
//reads an incoming int from the raspberry via serial
int readInt(){
  int num=0;
  Serial.println("in readInt");
  for(int i=0;i<3;i++){
    while (PiSerial.available() == 0);
    int b=PiSerial.read();
    num=((num>>8) | (b<<((3-1)*8)));
  }
  if (num>=(std::pow(2,(3*8-1)))){
    num-=std::pow(2,(3*8));
  }
  Serial.println(num);
  return num;
}

void steer(int percentage){
  steerPercentage=percentage;
}
//Send packet containing all data collected by the ESP to the Raspberry Pi via Serial protocol
void sendPacket() {
  int checkSum=1;
  PiSerial.write('E'); //1
  PiSerial.write('S'); //2
  PiSerial.write('P'); //3
  int conn_state_t=conn_state;
  PiSerial.write(conn_state_t); //4
  checkSum+=(conn_state_t%256);
  int absYaw_t=absYaw;
  sendInt(absYaw_t); //8
  checkSum+=(absYaw_t%256);
  int posL_t=posL;
  sendInt(posL_t); //12
  checkSum+=(posL_t%256);
  int posR_t=posR;
  sendInt(posR_t); //16
  checkSum+=(posR_t%256);
  int vMode_t=vMode;
  PiSerial.write(vMode_t); //17
  checkSum+=(vMode_t%256);
  int sMode_t=sMode;
  PiSerial.write(sMode_t); //18
  checkSum+=(sMode_t%256);
  int speed_t=speed;
  sendInt(speed_t); //22
  checkSum+=(speed_t%256);
  int log_var_t=log_var;
  sendInt(log_var_t); //26
  checkSum+=(log_var_t%256);

  checkSum%=256;
  sendInt(checkSum); //30 bytes per packet


  log_var++;
}
//main loop
void loop() {
  int t=millis();
  BNO08x_RVC_Data heading;
  // log_var=t-heartBeatT0;
  //checks if there is new gyro data available, if yes, updates internal absyaw variable. Also prevents the gyro from looping around
  if (rvc.read(&heading)) {
    newYaw=heading.yaw*10; //data is in .1 degrees, 1.4° error/360° (over)
    
    if(newYaw-lastYaw>1800) {yawOffset-=3600;}
    if(newYaw-lastYaw<-1800){yawOffset+=3600;}
    
    absYaw=(int)((newYaw+yawOffset)/(1+(float)gyroError/3600));
    if(abs(absYaw-lastAbsYaw)>2) {
      // Serial.print("gyro error ");
      // Serial.println(gyroError);
      // Serial.print("absyaw ");
      // Serial.println(absYaw);
    }
    arcSpeed=absYaw-lastAbsYaw;
    lastYaw=newYaw;
    lastAbsYaw=absYaw;
    sendPacket();
  } else{
    // Serial.println("no data");
  }
  if (PiSerial.available()){
    int command=PiSerial.read();  
    if (conn_state==STATUS_CONNECTED){
      switch(command){
        case CMD_STEER:
          steer(readInt());
          break;
        case CMD_SET_SERVO_CENT:
          SERVO_CENT=readInt();
          break;
        case CMD_SET_SERVO_MAX:
          SERVO_MAX=readInt();
          break;
        case CMD_SET_SERVO_MIN:
          SERVO_MIN=readInt();
          break;
        case CMD_SET_GYRO_P:
          kPY=readInt();
          break;
        case CMD_SET_GYRO_D:
          kDY=readInt();
          break;
        case CMD_SET_SPCTRL_P:
          kP=readInt();
          break;
        case CMD_SET_SPCTRL_D:
          kD=readInt();
          break;
        case CMD_SET_SPCTRL_I:
          kI=readInt();
          break;
        case CMD_SET_ARCCANCEL:
          arcCancel=(readInt()==1);
          break;
        case CMD_SET_GYROERROR:
          Serial.print("SET GYROEEROR ");
          
          gyroError=readInt();
          Serial.println(gyroError);
          break;
        case CMD_SET_HANDBRAKE_P:
          handbrakeP=readInt();
          break;
        case CMD_SET_ARCDIR:
          arcDirection=readInt();
          break;
        case CMD_SET_GYRO_L_MILLIS:
          gyroLatencyMillis=readInt();
          break;
        case CMD_SET_SGYRO_LIMITS:
          sGyroLimits=readInt();
          break;
        case CMD_HEARTBEAT:
          //resets last heartbeat 
          conn_state=STATUS_CONNECTED;
          setLedStatus(STATUS_CONNECTED);
          heartBeatT0=millis();
          // Serial.println(speed);
          break;
        case CMD_SET_VMODE:
        {
          Serial.println("set vmode");
          int data=readInt();
          //checks if vmode is valid
          if(data==V_FORWARD || data==V_BACKWARD || data==V_BRAKE || data==V_STOP || data==V_UNREGULATED || data==V_HANDBRAKE){
            if(data==V_HANDBRAKE) {
              handbrakePos0=posR;
              handbrakeIntegral=0;
            }
            vMode=data;
            
          }
        }
          break;
        case CMD_SET_TARGETSPEED:
          targetSpeed=readInt();
          break;
        case CMD_SET_SMODE:
        {
          int data=readInt();
          Serial.println("smode");
          if(data==S_ARC) {
            isArcing=true;
            arcCancel=false;
            Serial.println("sarc");
            Serial.println(absYaw);
          }
          if(data==S_NONE || data==S_GYRO || data==S_ARC){
            sMode=data;
          }
        }
          break;
        case CMD_SET_BREAKPERCENT:
          brakePowerPercent=readInt();
          break;
        case CMD_SET_TARGET_YAW:
          targetYaw=readInt();
          Serial.println("tyaw set");
          Serial.println(targetYaw);
          break;
        case CMD_SET_UNREG:
          Serial.println("set unreg");
          unregPower=readInt();
          break;
      }
    } else {
      if (command==CMD_HEARTBEAT){
        //resets last heartbeat 
          conn_state=STATUS_CONNECTED;
          setLedStatus(STATUS_CONNECTED);
          heartBeatT0=millis();
      }
    }
    
  }
  int hb=heartBeatT0;
  //Heartbeat detetction, if the raspberry hasn't sent a hearrtbeat command in .5 seconds it assumes the program on the pi may have crashed or stopped
  if((conn_state==STATUS_CONNECTED) && (t-hb)>500) {
    Serial.println("disconnect!");
    disconnect();
  }
  if(t-lastUSread>US_DELAY){
    // sendUSPulse();
    lastUSread=t;
  }

}

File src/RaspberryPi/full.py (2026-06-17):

#! /usr/bin/python
'''The main python file, it contains the code for both robot runs and helper functions'''
from dataclasses import dataclass
import json
from math import acos, asin, cos, degrees, pi, atan, ceil, copysign, floor, sin, sqrt, tan
import os
import multiprocessing as mp
import random
import threading
from time import sleep, time
from log import *
from utilities import func_thread
from sys import argv

import cv2
from picamera2 import Picamera2

run_type = None
#full_wro.service

def assignArgs(args: list) -> None:
    global run_type
    for i in args:
        match i:
            case "-obs":
                run_type = "Obstacle"
            case "-ope":
                run_type = "Open"
            case "-tst":
                run_type = "Test"
            case "-2nd":
                run_type = "2nd day"
            case _:
                log.error(f"System argument {i} is not recognized")
                log.save_logs_to_file()
                log.save_temp_logs_to_file()
             

if len(argv) > 1:
    assignArgs(argv[1:])
    with open(directory / "args.txt","w") as file:
        for i in argv[1:]:
            file.write(i+"\n")
else:
    with open(directory / "args.txt","r") as file:
        args = file.readlines()
        args = [i.replace("\n","") for i in args]
    assignArgs(args)


TURNTARGET_INNER=0
TURNTARGET_INNER_OBS=1
TURNTARGET_MIDDLE=2
TURNTARGET_OUTER_OBS=3
TURNTARGET_OUTER=4
TURN_RADIUS=12
turnDists=[94, 74, 64, 54, 34] #94->98
laneWallDists=[20, 40, 50, 60, 80]
'''Indexed by lane (left/right). 0:left,..,4:right'''
def angularToXy(angle:int, distance:int):
    '''Helper method to convert angular (angle distance) coordinates into x and y coordinates'''
    x=distance*sin(angle/180*pi)
    y=distance*cos(angle/180*pi)
    return x,y

def XyToAngular(x:int,y:int):
    '''Helper method to convert x and y coordinates into angle and distance'''
    if x==0 or y==0: return 0, y
    angle=atan(x/y)
    distance=x/sin(angle)
    angle=angle/pi*180
    return angle,distance
@dataclass
class Object:
    '''Dataclass representing a detected object'''
    objStart:tuple[float,float]
    '''The leftmost point of the object'''
    objEnd:tuple[float,float]
    '''The rightmost point of the object'''
    relToAbsX:int=-1
    relToAbsY:int=-1
    angle:float=-1
    '''The rotation of the object (relative to the walls)'''
    def getCenter(self)->tuple[int,int]:
        '''Getter method of 'center' property
        
        Returns the center of the detected object (average of objStart and objEnd)'''
        return ((self.objStart[0]+self.objEnd[0])/2,(self.objStart[1]+self.objEnd[1])/2)
    center=property(getCenter,None,None)
    '''Returns the center of the detected object (average of objStart and objEnd)'''
    def isEmpty(self)->bool:
        '''Getter method of 'empty' property
        
        True if object was not found'''
        return True if self.objStart[0]==-1 else False
    empty=property(isEmpty,None,None)
    '''True if object was not found'''
    
    def toAbsolute(self):
        '''Returns this object converted to absolute position'''
        objStartAbs=[self.objStart[0]+self.relToAbsX,self.objStart[1]+self.relToAbsY]
        objEndAbs=[self.objEnd[0]+self.relToAbsX,self.objEnd[1]+self.relToAbsY]
        return Object(objStartAbs,objEndAbs)
    def toRelAngle(self):
        relStartAngle,startDist=XyToAngular(*self.objStart)
        relEndAngle,endDist=XyToAngular(*self.objEnd)
        relStartAngle-=self.angle
        relEndAngle-=self.angle
        return Object(angularToXy(relStartAngle,startDist),angularToXy(relEndAngle,endDist),angle=0)
    def toRelative(self):
        '''Returns this object converted to relative position'''
        objStartRel=[self.objStart[0]-self.relToAbsX,self.objStart[1]-self.relToAbsY]
        objEndRel=[self.objEnd[0]-self.relToAbsX,self.objEnd[1]-self.relToAbsY]
        return Object(objStartRel,objEndRel)
    
CAMERA_ANGLE_OFFSET=0 #how much (degrees) the camera is rotated to the left relative to the robot
HORIZONTAL_FOV=53.1
VERTICAL_FOV=41.49
CAMERA_VERTICAL_TILT=9.5 #10.76
cameraPos=(0,-4,19.5)
GREEN=1
'''Constant for the color Green. Used for obstacle color detection and storing.'''
RED=2
'''Constant for the color Red. Used for obstacle color detection and storing.'''
RMG_BORDER=0 #red-green

ANALYSE_NTH_PIXELS=4
'''Analyse every this many pixel'''

def mapPointToCam(point:tuple[int,int,int])-> tuple:
    log.debug("mapPointToCam %s %s %s"%point)
    px=320+(degrees(atan((point[0])/(point[1]-cameraPos[1])))+CAMERA_ANGLE_OFFSET)*(640/HORIZONTAL_FOV)
    # print(degrees(atan((point[2]-cameraPos[2])/(point[1]-cameraPos[1]))))
    # print((point[2]-cameraPos[2]))
    # print((point[1]-cameraPos[1]))
    # print(degrees(atan((point[2]-cameraPos[2])/(point[1]-cameraPos[1]))))
    # py=240-(degrees(atan((point[2]-cameraPos[2])/(point[1]-cameraPos[1])))+11.5)*(480/44)
    py=240-(degrees(atan((point[2]-cameraPos[2])/(point[1]-cameraPos[1])))+CAMERA_VERTICAL_TILT)*(480/VERTICAL_FOV)
    if px<0: px=0
    if px>=640: px=639
    if py<0: py=0
    if py>=480: py=479
    return (px,py)
camQueue = mp.Queue(10)
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

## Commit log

2026-02-11 added last year's documentation + engineering journal
    [Camera final.f3d, Camera final.stl, Camera stand 2 v1.f3d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]
2026-02-22 added January's angineering journal
    [engineering_journal.xlsx]
2026-06-22 first draft of mechanical and sensor documentation
2026-06-22 added missing journal entries
    also updated flowcharts
2026-06-22 Uploaded new 3D models
    [bumper_mount.f3d, bumper_mount.stl, glove.stl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]
